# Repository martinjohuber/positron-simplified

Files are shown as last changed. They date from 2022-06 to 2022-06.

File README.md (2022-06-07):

This repository is a fork of the Positron printer by @KRALYN and all credit goes to him!

I love the idea of the Positron being a small and portable printer build in a completely new way. But I wanted to make it much simpler and more accessible to more people so I changed the design from scratch to only use standard parts and some laser cut POM plates.

I did the first successfull print with this design and now it needs further optimization and that is why I am sharing the design. First things to improve would be the print volume, extruder and housing.

I hope that I can help with my version of the Positron to bring this kind of printer to a broader audience. 

I am the CTO of a 3D-Printer manufacturer but this is a private project for me because I still love to build new types of printers in my spare time. If anybody wants to discuss what it takes to bring this printer to the market dont hesitate to contact me.

Here is the original github project from KRALYN:

# PositronV3 LINKS:::

[Positron 3D Website](https://positron3d.com)

[Subscribe for Kit Availability](https://docs.google.com/forms/d/e/1FAIpQLScSUN6uIbf_p_ZukdroXxWQURiDlr32UO7YCeqWrKqZagVfdA/viewform)

[Inquire about Producing Kits](https://forms.gle/fReHdo7zMeWoU7ML7)

[Check out our Youtube to see it in action!](https://www.youtube.com/watch?v=X_QLxTVtyng)

[Source Parts and links from here (BOM)](https://docs.google.com/spreadsheets/d/1M--jvOxUEVNc-NtEsor3uPZQsdXsPD1CKWxmc8fwLWI/edit?usp=sharing)

[PositronV3 Manufacturing & production Misc notes](https://docs.google.com/document/d/1z848gDqvVRCHIMzX_ltr0iuHKC0EaDqbpCQJTiSfUPk/edit?usp=sharing)



Upside-down, compact, portable, and super fast 3D printer - `Positron V3` has it all. A compact 3D printer that packs into a filament spool box, so you can take it anywhere you want. This design is looking at a 3D printer less like a stationary machine, but more like a powerful tool in a maker/inventor's tool kit. The printer deploys and folds up in less than 90 seconds, fits easily inside a bag, and prints at 200+mm/s.

**Specs**: 
- Max Print Speed: `250mm/s`
- Max Travel Speed: `350mm/s`
- Acceleration: `9800mm/s^2`
- Build Volume: `180x185x180mm`
- Weight: `2700-3100g`
- Hotend max temp: `250C`
- Build Plate Max temp: `90C`
- Power supply: `19-24V; 150-220W`

> Do not treat this design as a finished product. Instead, please see it as a project to be improved upon. When you make this, if you find any improvements, please share it with the community! I could easely have overlooked things; Lets make this printer the best it can be!
>**Disclaimer**: `Positron V3` design is a ***functional*** prototype, not a complete product. **There is absolutely no warranty, and you will make this design at your ***OWN*** risk. I will not be responsible for any damages associated with this design**. 
If you like the design, please consider supporting my work via [Patreon](https://www.patreon.com/KRALYN3D)
Or make a donation through [Paypal](https://www.paypal.com/donate/?hosted_button_id=D6APYZU6RKY6S)

# Licenses



**License usage**: `CC-BY`

If you are manufacturing this 3D printer or a close derivative, please put `Positron Logo` visibily on your product and designate `Positron3D` as the inventor of this product. You can find the file inside the logos folder.

On any online postings for any Parts or Kits, please be sure to link back to this github page, as well as to Positron 3D's website.
`https://github.com/KRALYN/PositronV3`
`https://positron3d.com/`

If you made a profit from this design, please consider donating a portion to `Positron3D`. I will be exceedingly grateful.

***All hardware materials and designs provided here are licensed under the [CC-BY-SA-4.0](https://creativecommons.org/licenses/by-sa/4.0/) hardware license.
All documentation, including the Wiki, is under the Creative Commons [CC-BY-SA-4.0](https://creativecommons.org/licenses/by-sa/4.0/) license***.

<div align="center">
Open Licenses
</div>

[Top](#positronv3)

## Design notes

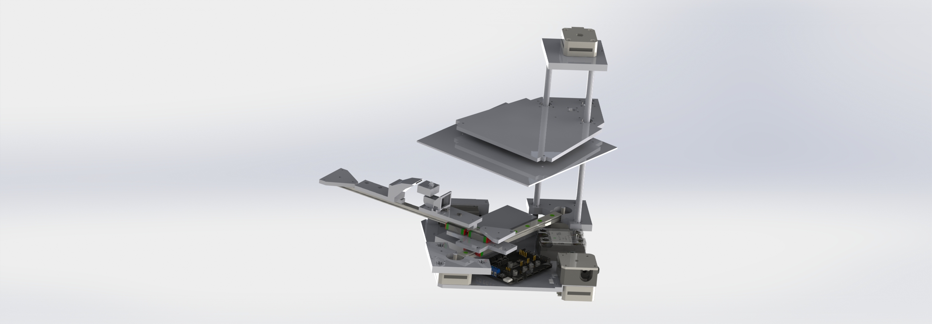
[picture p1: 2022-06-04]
CAD files/FirstRender.JPG

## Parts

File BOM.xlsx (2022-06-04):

Quantity | Description | Source | Price | Price total | Link | alternative Link
3 | Nema 17 stepper motor 20 mm | Amazon/Stepperonline | 10 | 30 | https://www.amazon.de/gp/product/B06XVM38YW/ref=ppx_yo_dt_b_asin_title_o08_s00?ie=UTF8&psc=1
1 | Nema 17 stepper motor 25 mm for Z axis | Amazon/Stepperonline | 10 | 10
1 | 24 V Power Supply |  | 22 | 22 | https://www.amazon.de/gp/product/B09Q94Q3SL/ref=ppx_yo_dt_b_asin_title_o04_s00?ie=UTF8&th=1
1 | right angled piping piece to mount the hotend and act as a cooling block, needs to be machined |  | 15 | 1.5 | https://www.amazon.de/gp/product/B07YJWQ1YR/ref=ppx_yo_dt_b_asin_title_o06_s00?ie=UTF8&psc=1
1 | MGN12H 200mm linear rail should be changed to MGN12C to improve build volume | Amazon/Aliexpress |  | 15
1 | MGN9H with two carriages should be changed to MGN9C to improve build volume | Amazon/Aliexpress |  | 15
2 | Idler Pulleys with 20 teeth 5 mm bore |  | 1 | 2 | https://de.aliexpress.com/item/4000187126436.html
4 | Idler Pulley no teeth 5 mm bore |  | 1 | 4 | https://de.aliexpress.com/item/4000187126436.html
2 | Pulleys 20 teeth for nema 17 motors |  | 0.5 | 1 | https://de.aliexpress.com/item/32819729978.html
1 | e3d titan extruder should probably be exchanged for a BMG style extruder or orbiter for more pushing force |  |  | 10
1 | IEC Socket |  | 1 | 1 | https://de.aliexpress.com/item/4000469723664.html
2 | 30 mm fans to cool the power supply and the electronics |  |  | 2
1 | SKR pico |  | 40 | 40 | https://www.amazon.de/gp/product/B09VL3MM5V/ref=ppx_yo_dt_b_asin_title_o01_s00?ie=UTF8&th=1
1 | Raspberry Pi 3 Model A+ |  |  | 30
1 | SSR Relay 230 V |  | 16 | 8 | https://www.amazon.de/gp/product/B09N9BCBQT/ref=ppx_yo_dt_b_asin_title_o03_s00?ie=UTF8&psc=1
2 | 5015 fans |  |  | 5
3 | 8 mm rods with M4 threads for mounting |  |  | 12
3 | LMLUU bearing |  |  | 5
1 | spindle |  |  | 5
1 | nut for spindle |  |  | 1
1 | coupler for spindle and nema 17 |  |  | 2
3 | springs for the build plate |  |  | 1
3 | adjusting knobs |  |  | 1
1 | build plate from 2 mm aluminium |  |  | 3
1 | magnetic PEI sheet |  | 30 | 30 | https://www.amazon.de/gp/product/B09SXRJWSN/ref=ppx_yo_dt_b_asin_title_o03_s00?ie=UTF8&psc=1
1 | heat pad 100 Watts 220 V 120*120 |  | 2.5 | 2.5 | https://de.aliexpress.com/item/32825087275.html
1 | insulation pad |  | 9 | 4.5 | https://www.amazon.de/gp/product/B08L7R1ZMT/ref=ppx_yo_dt_b_asin_title_o03_s00?ie=UTF8&th=1
1 | e3d style nozzle |  |  | 1
1 | heating block |  |  | 1
1 | heater cartride 24 V 40 Watts (better 30 Watts) |  |  | 2
1 | temperature sensor |  |  | 1
5 | feet |  |  | 2
1 | gt2 timing belt |  | 10 | 1 | https://de.aliexpress.com/item/32606449444.html
 | a lot of cables and screws
 |  |  |  | 271.5

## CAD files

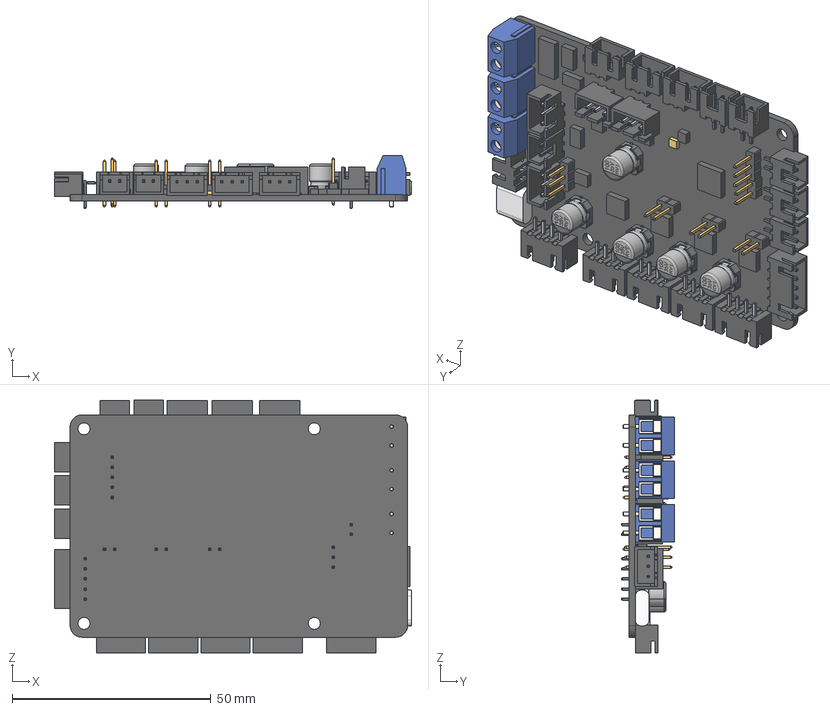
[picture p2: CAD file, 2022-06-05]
CAD files/Individual CAD Files/SKR PICO Mockup Assembly v1.step
89.9 x 13.4 x 63.6 mm
BTT SKR MINI V2_JST 2pin x 6
BTT SKR MINI V2_100uF 35V 6.3x7 x 5
BTT SKR MINI V2_Header 3 pin (2) x 8
Terminal Screw x 3
B4B-XH-A (BODY) x 5
B4B-XH-A (PIN) x 20
Molex 5Pin - 2.54mm v1
3 pin 2.54 x 2
BTT SKR MINI V2_2 Pin connector x 5

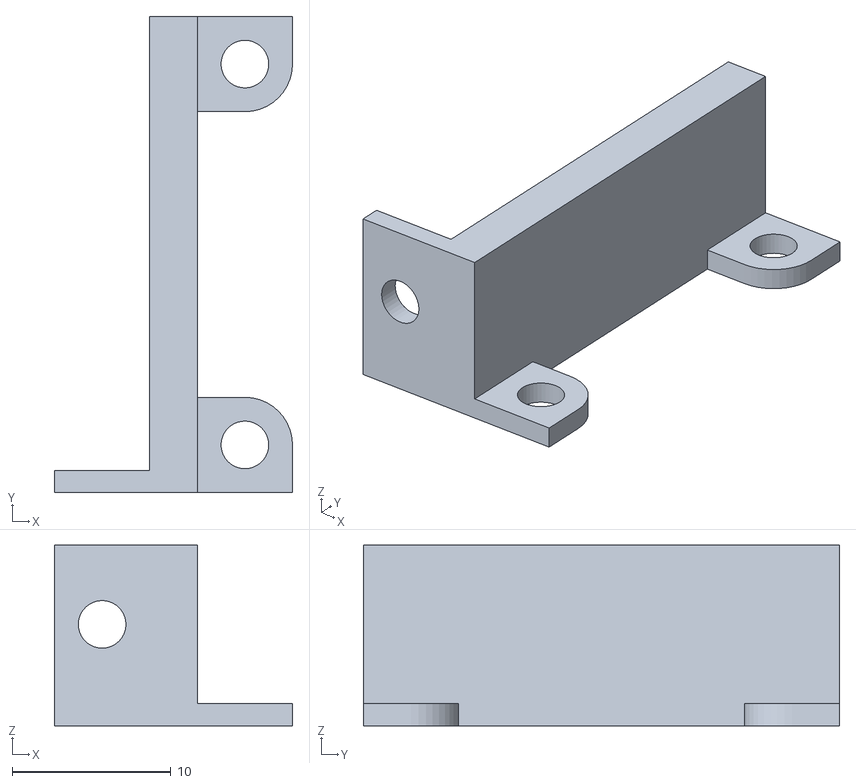
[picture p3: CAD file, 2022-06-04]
CAD files/3D printed Parts/30mmfanholderhalf.STL
15.0 x 30.0 x 11.4

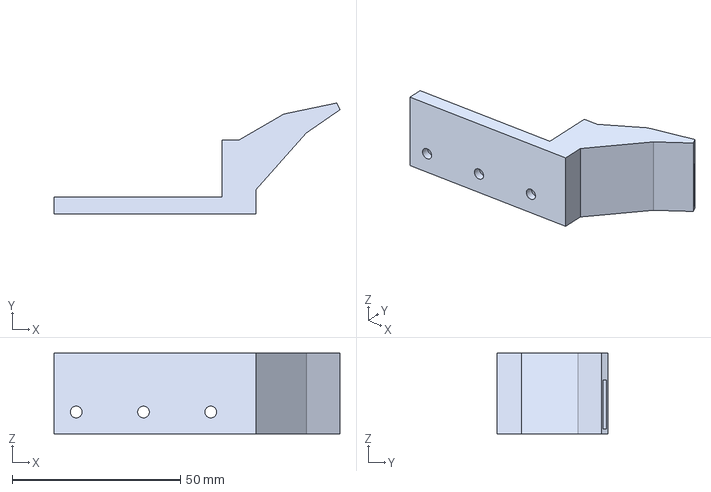
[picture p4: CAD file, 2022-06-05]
CAD files/Individual CAD Files/Cooling and Hotend/Cooling_Nozzle.stp
85.0 x 33.0 x 24.0 mm

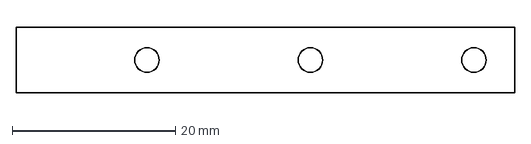
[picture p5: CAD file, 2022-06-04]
CAD files/Lasercut parts/SpacerHotend_5mm_POM.DXF
61.0 x 8.00 mm

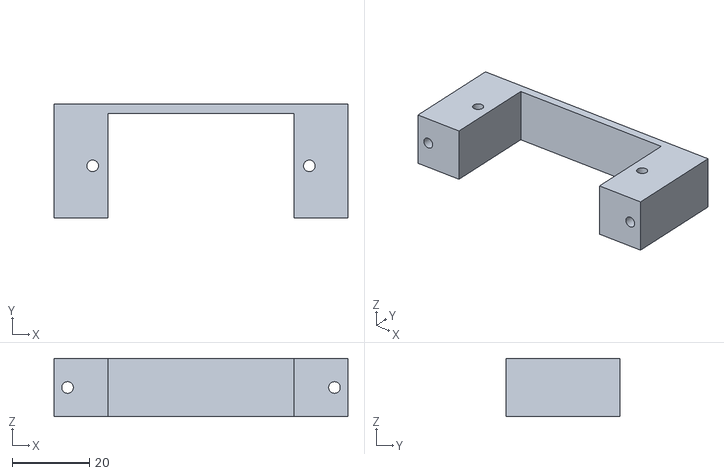
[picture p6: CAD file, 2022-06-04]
CAD files/3D printed Parts/SocketHolder.STL
76.0 x 29.5 x 15.0

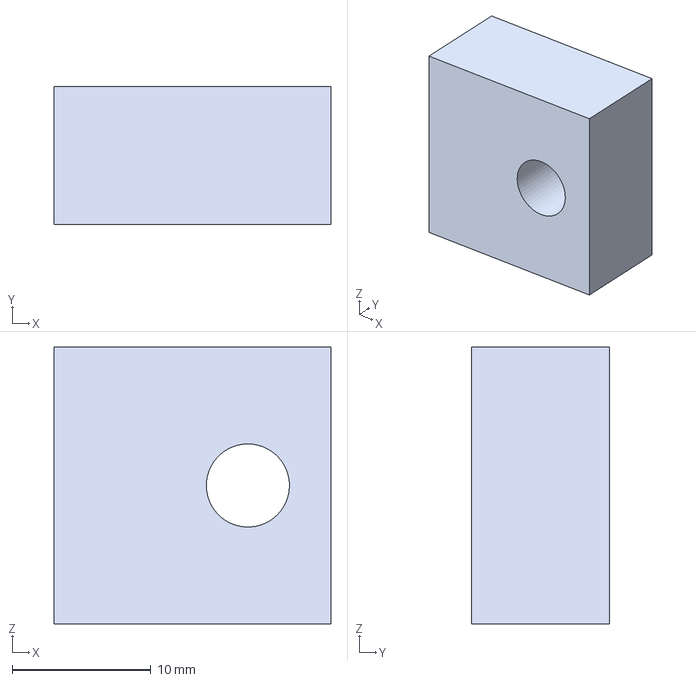
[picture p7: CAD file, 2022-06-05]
CAD files/Individual CAD Files/Cooling and Hotend/Heatblock.stp
20.0 x 10.0 x 20.0 mm

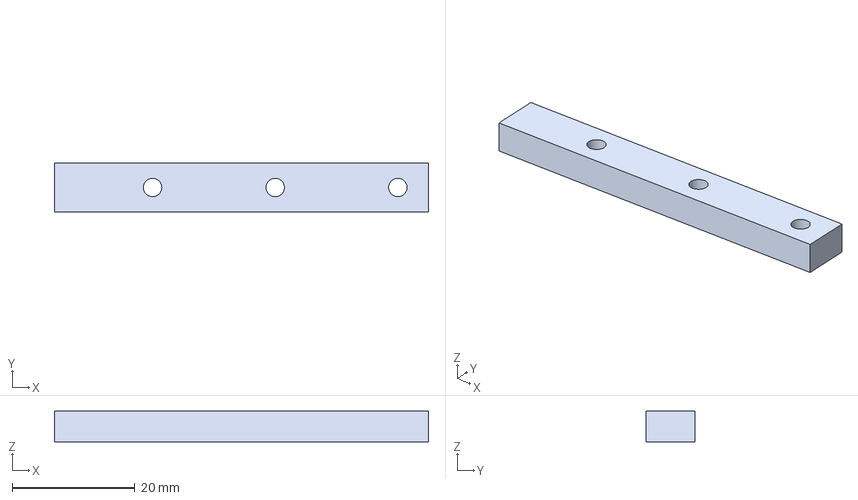
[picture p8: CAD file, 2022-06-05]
CAD files/Individual CAD Files/SpacerHotend.stp
61.0 x 8.00 x 5.00 mm

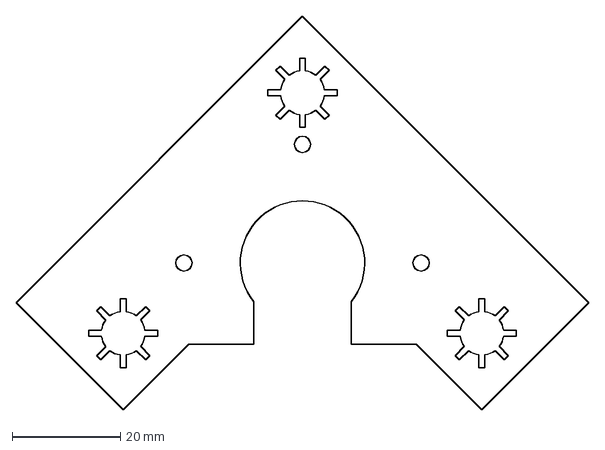
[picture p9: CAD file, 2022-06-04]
CAD files/Lasercut parts/Motorplate_9mm_POM.DXF
105.9 x 72.8 mm

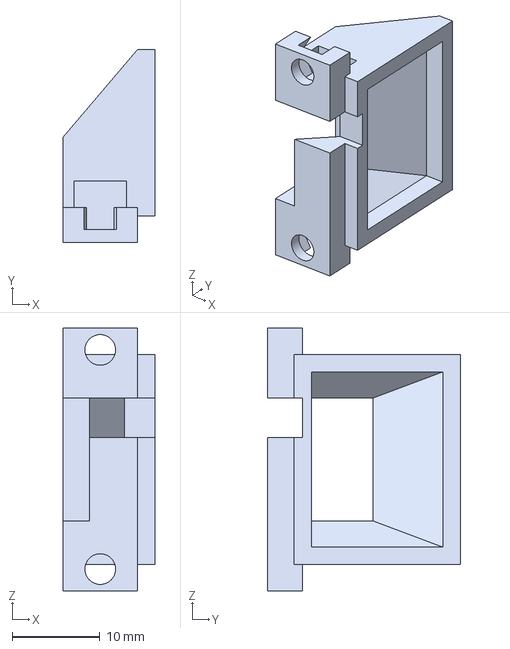
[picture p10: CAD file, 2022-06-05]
CAD files/Individual CAD Files/Cooling and Hotend/Cooling_Block.stp
10.5 x 22.0 x 30.0 mm

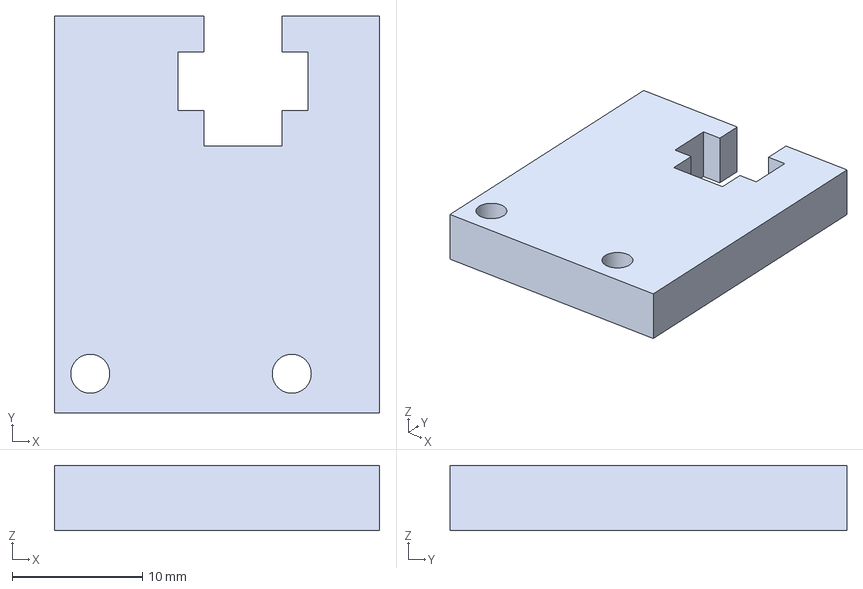
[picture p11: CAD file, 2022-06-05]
CAD files/Individual CAD Files/EndstopZ.stp
25.0 x 30.5 x 5.00 mm

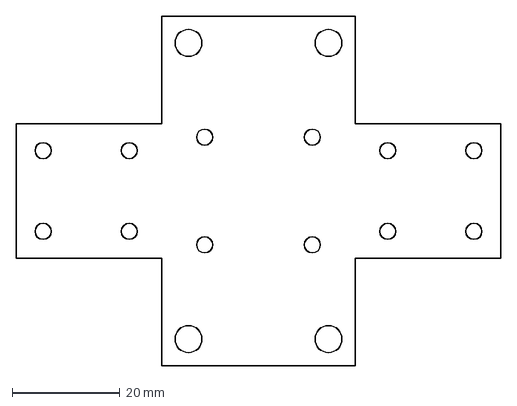
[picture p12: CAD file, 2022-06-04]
CAD files/Lasercut parts/Carrriage1_5mm_POM.DXF
90.0 x 65.0 mm

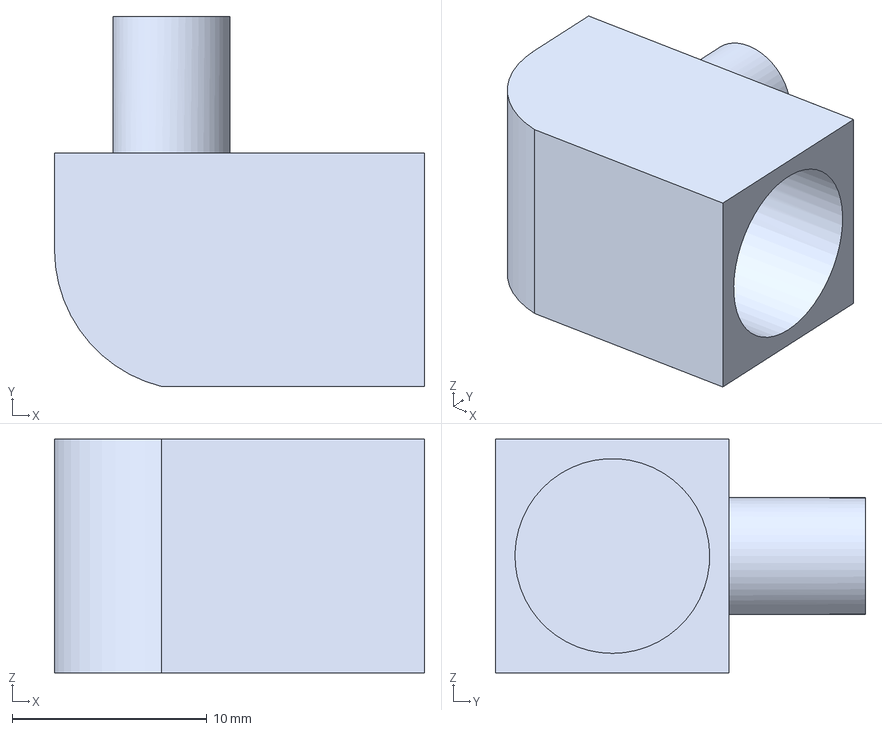
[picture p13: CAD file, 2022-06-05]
CAD files/Individual CAD Files/Cooling and Hotend/Heatsink.stp
19.0 x 19.0 x 12.0 mm

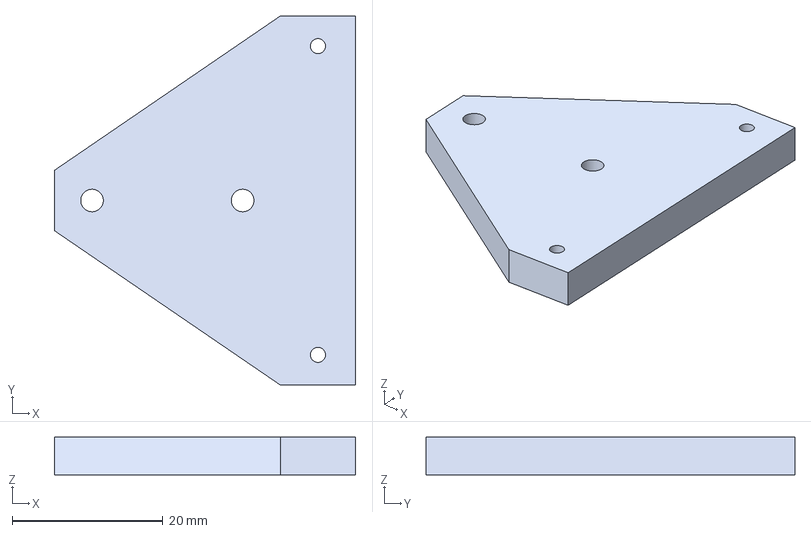
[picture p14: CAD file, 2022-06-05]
CAD files/Individual CAD Files/TBeltHolder.stp
40.0 x 49.0 x 5.00 mm

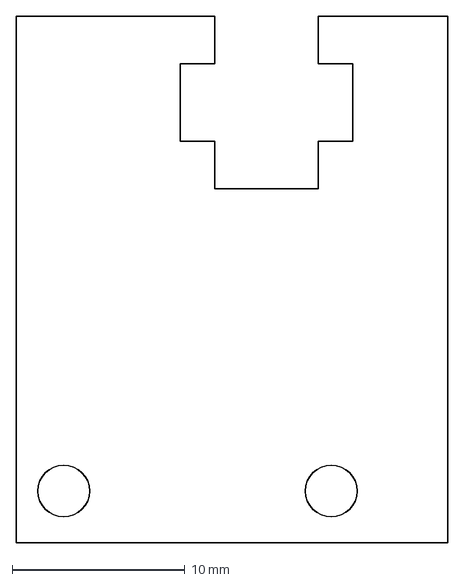
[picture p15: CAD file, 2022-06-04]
CAD files/Lasercut parts/EndstopZ_5mm_POM_securedbyhammernut.DXF
25.0 x 30.5 mm

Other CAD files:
CAD files/Individual CAD Files/30mmfanholderhalb.stp
CAD files/3D printed Parts/Cooling_Nozzle.STL
CAD files/3D printed Parts/Cooling_Block.STL
CAD files/Individual CAD Files/Zplate.stp
CAD files/Individual CAD Files/24VPowerSupply.stp
CAD files/Individual CAD Files/Baseplate.stp
CAD files/Individual CAD Files/BuildplateNew.stp
CAD files/Individual CAD Files/Carrriage1.stp
CAD files/Individual CAD Files/Motorplate.stp
CAD files/Individual CAD Files/Nema 17 20mm Front facing.stp
CAD files/Individual CAD Files/PPPlate.stp
CAD files/Individual CAD Files/Power inlet v2.step
CAD files/Individual CAD Files/PrintPlateAlu.stp
CAD files/Individual CAD Files/SocketHolder.stp
CAD files/Individual CAD Files/TPulleyHolder.stp
CAD files/Lasercut parts/Baseplate_5mm_POM.DXF
CAD files/Lasercut parts/BuildplateNew_5mm_POM.DXF
CAD files/Lasercut parts/ExtruderHolder_3mm_Acryl.DXF
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

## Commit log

2022-06-04 included thickness and material in name
    [Baseplate_5mm_POM.DXF, BuildplateNew_5mm_POM.DXF, Carrriage1_5mm_POM.DXF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]
2022-06-04 changed names to english
    [30mmfanholderhalf.STL, Cooling_Block.STL, Cooling_Nozzle.STL]
2022-06-05 Added individual CAD Files
    [24VPowerSupply.stp, 30mmfanholderhalb.stp, Baseplate.stp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]
